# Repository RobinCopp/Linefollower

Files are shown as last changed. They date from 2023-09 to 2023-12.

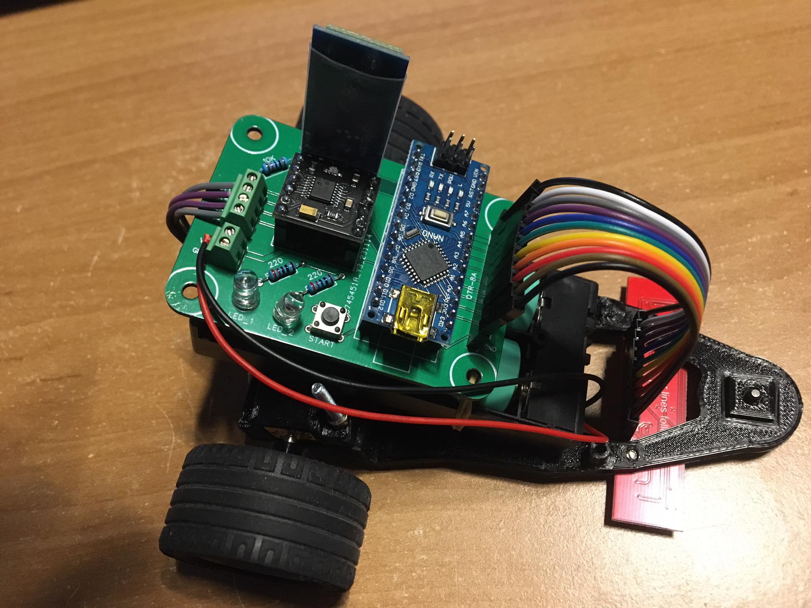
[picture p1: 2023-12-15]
images/367906358_393842836311221_281321537537603859_n.jpg

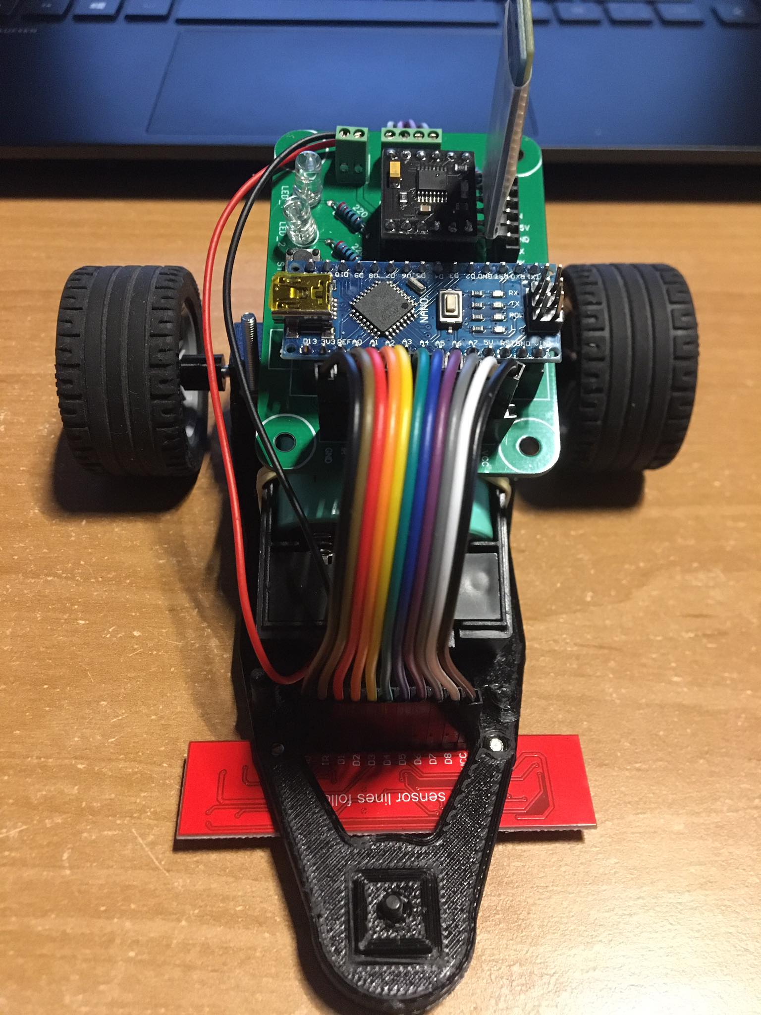
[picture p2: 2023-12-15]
images/385540789_1121335352184012_5968842558492933345_n.jpg

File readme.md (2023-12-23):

# LineFollower



## specifications

microcontroller: Arduino Nano imitatie (ATmega 328P)

motors: Micro Metal Gearmotors (6V 50:1)

h-bridge: DRV8833

sensors: QTR-8A

batteries: 18650 li-ion (2x)

wireless communication: HC-05

distance sensor - motors: 85 mm

weight: 231 g

speed: 0,7 m/s

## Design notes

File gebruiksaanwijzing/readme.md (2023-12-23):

# Gebruiksaanwijzing

### opladen / vervangen batterijen
De twee 18650 li-ion batterijen hebben een speciale oplader nodig. Probeer deze nooit op te laden met een oplader die hier niet voor bedoeld is, dit kan serieuze schade aanrichten.
De batterijhouder wordt op zijn plaats gehouden door enkele elastiekjes. Door deze voorzichtig los te maken kan de batterijhouder van onder de printplaat gehaald worden. Als dit gebeurd is kunnen ze uit de houder gehaald worden en in de oplader gestoken worden. Het is natuurlijk van belang dat de batterijen in de juiste richting in zowel de oplader als in de batterijhouder worden geïnstalleerd. Om de batterijhouder met opgeladen batterijen terug in de auto te installeren moeten de vooraf gaande stappen gewoon in de omgekeerde volgorde uitgevoerd worden.

### draadloze communicatie
#### verbinding maken
Voor draadloze connectie met de auto is een bluethooth module op de auto voorzien. Let op! De bleuthooth module kan niet met Apple apparaten gebruikt worden. Zorg dus dat je een Android toestel ter beschikking hebt. Verder heb je de app "Serial Bluetooth Terminal" nodig om commando's naar de auto te sturen. Verbind eerst via de instellingen van uw apparaat met de bluethoothmodule en selecteer deze vervolgens in de app. Hierna is alles klaar voor het gebruik van draadloze communicatie.

#### commando's
debug [on/off]  = Geeft de ingestelde parameters weer

run  = Starten van de auto (begint te rijden)

stop  = Stoppen van de auto

set cycle [µs]  = Een tijd instellen hoelang de cyclus mag duren. Ongeveer dubbel de calculation time. Deze wordt weergegeven bij debug

set power [0..255]  = Vermogen instellen van de motoren, zet dit niet zomaar op max, de auto zal enkel wheelies trekken

set diff [0..1]  = Het snelheids verschil van de auto tussen de rechte stukken en de bochten. Hoe hoger, hoe minder de auto in de bochten vertraagd

set kp [0..]  = Dit heeft een invloed op hoe "agressief de auto instuurt". Als deze te hoog staat zal de auto heen en weer over de lijn schokken

set ki [0..]  = Zal meer bijsturen hoelanger de bocht

set kd [0..]  = Corrigeert "kp", hoe groter de fout bij "kp", hoe meer er wordt gecorigeerd

calibrate black  = moet uitgevoerd worden als de sensor op een zwart oppervlak staat, hierdoor weet de auto wat zwart is en wat hij straks zal moeten volgen

calibrate white  = moet uitgevoerd worden als de sensor op een wit oppervlak staat, hierdoor weet de auto wat wit is

### kalibratie
Kalibratie moet uitgevoerd worden voor de auto begint te rijden, en moet op het zelfde soort oppervlak gebeuren als de auto straks op zal rijden en moet op de correcte kleur gebeuren, niet op een kleur die er een beetje op trekt.

Eenmaal de auto op de correcte kleur staat, stuur de commando's "calibrate black" en "calibrate white" door naar de auto zoals in de vorige rubriek uitgelegd.

### settings
De robot rijdt stabiel met volgende parameters:

cycle time: 3000

power: 72

diff: 0.74

kp: 20

ki: 0

kd: 0.90

### start/stop button
Na de batterijspanning aan te leggen met de schakelaar die zich vooraan op de batterijhouder bevindt kan op de startknop gedrukt worden om de auto te doen rijden. Deze bevindt zich langs de rechterkant in het midden van de printplaat. Als u erin slaagt om op dezelfde knop te drukken terwijl de auto aan het rijden is, zal deze knop de auto ook weer doen stoppen.

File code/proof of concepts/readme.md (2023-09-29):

# Proof of Concepts

Een proof of concept is een combinatie van minimale hard- en software om eenvoudig aan te tonen dat iets werkt.  
Proof of concepts kunnen enerzijds als eerste poging dienen om een bepaald onderdeel van het project werkend te krijgen. Anderzijds kunnen ze tijdens het debuggen van het finale project dienen als test om eventuele hardware problemen te elimineren bij onduidelijke problemen.
<br />  
<br />
Een proof of concept bestaat uit
* een elektronisch schema (indien van toepassing)
* minimale code om de voorop gestelde zaken te demonstreren
* minimale uitleg / aandachtspunten
<br />
De elektronische schakelingen van de proof of concepts komen bij voorkeur overeen met deze van de uiteindelijke linefollower, zodat de code zonder aanpassingen op het finale project kan draaien.

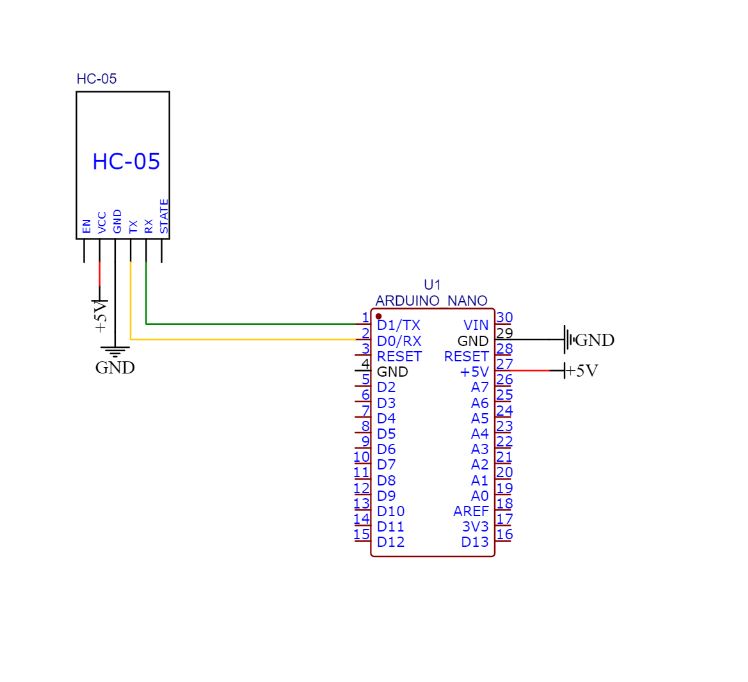
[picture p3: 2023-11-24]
code/proof of concepts/wireless communication/Bluetooth.JPG

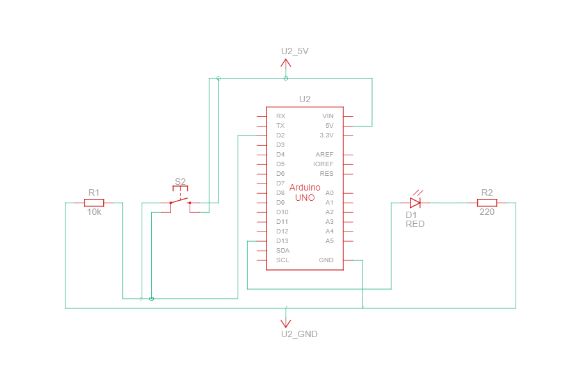
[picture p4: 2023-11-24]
code/proof of concepts/interrupt/Interrupt.JPG

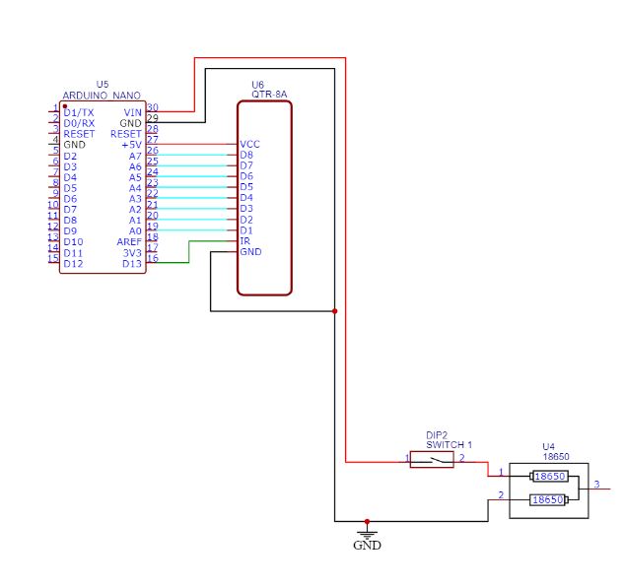
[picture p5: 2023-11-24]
code/proof of concepts/sensor/Sensoren_Schema.JPG

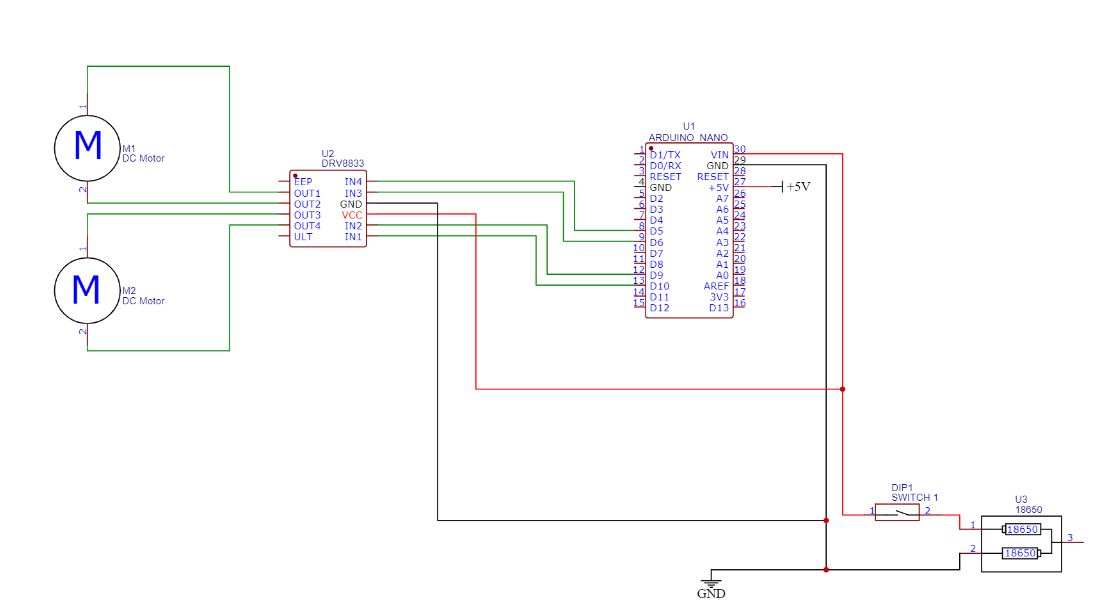
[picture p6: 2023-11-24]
code/proof of concepts/hbridge/H-Brug.JPG

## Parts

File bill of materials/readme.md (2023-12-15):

## bill of materials
<br />

|volgnummer|naam|omschrijving|nieuw/recup|kostprijs/stuk|aantal|subtotaal|
|---|----|---|---|---|---|---|
| 1|  Microcontroller | ATMega 328P |  Nieuw |  €2,61 |  1 | €2,61 |
| 2|  Sensoren  |  QTR-8A |  Nieuw |  €1,24 | 1 |  €1,24 |
| 3|  H-Brug  |  DRV8833 |  Nieuw |  €0,48 |  1 |  €0,48 |
| 4|  Motoren  |  Geared 6V 50:1 |  Nieuw | €3,25 |  2 | €6,50 |
| 5|  Bluethooth  | HC-05 |  Nieuw |  €3,90 | 1 | €3,90 |
| 6|  Batterij  | 18650 | Nieuw |  €3,50 |  2 |  €7 |
| 7|  Batterij Houder  |  Houder |  Recup |  €0 |  1 |  €0 |
| 8|  Batterij Oplader |  Oplader |  Nieuw |  €3,69 |  1 |  €3,69 |
| 9|  Weerstanden  |  10k en 220 |  Recup | €0 | 3 |  €0 |
| 10|  Led  |  Led |  Recup |  €0 |  2 |  €0 |
| 11|  Knop  |  Drukknop | Recup | €0 |  1 |  €0 |
| 12|  Kabels  |  Dupont kabels | Nieuw |  €1,25 |  1 |  €1,25 |
| 13|  Printplaat  |  Custom |  Nieuw |  €5 | 1 |  €5 |
| 14|  PinHeaders  | Pinheaders |  Nieuw |  €2,22 | 1 |  €2,22 |
| 15|  Wielen  |  Lego + 3Dprinted adapter |  Recup |  €0 | 2 | €0 |
| 16|  Chassis  |  3Dprinted |  Nieuw |  €0,65 |  1 |  €0,65 |
| 17|  Boutjes + Moertjes  | M3 | Recup |  €0 | 7 |  €0 |
| | | | | | TOTAAL |  €34,54 |

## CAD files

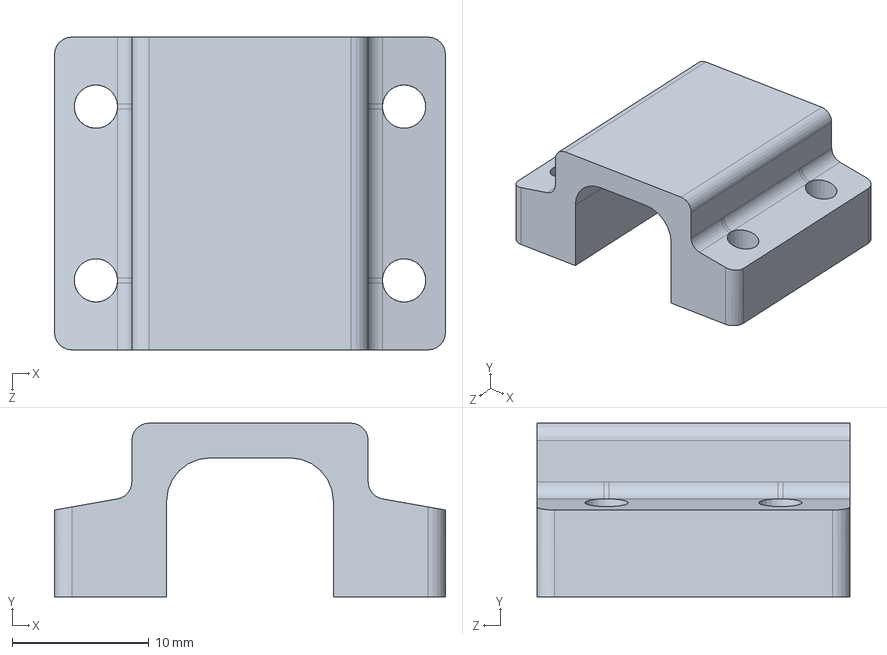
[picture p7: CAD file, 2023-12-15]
technische tekeningen/mechanisch/motor_mount_v2.1.1_straight.SLDPRT
28.6 x 12.7 x 22.9 mm

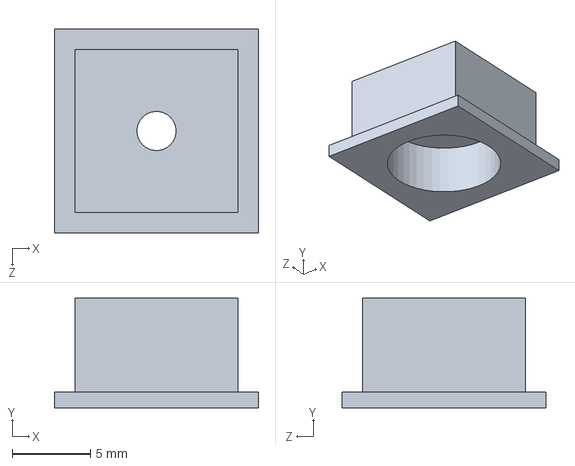
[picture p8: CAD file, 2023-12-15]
technische tekeningen/mechanisch/FRONT_LEG_ADAPTER.SLDPRT
13.0 x 7.00 x 13.0 mm

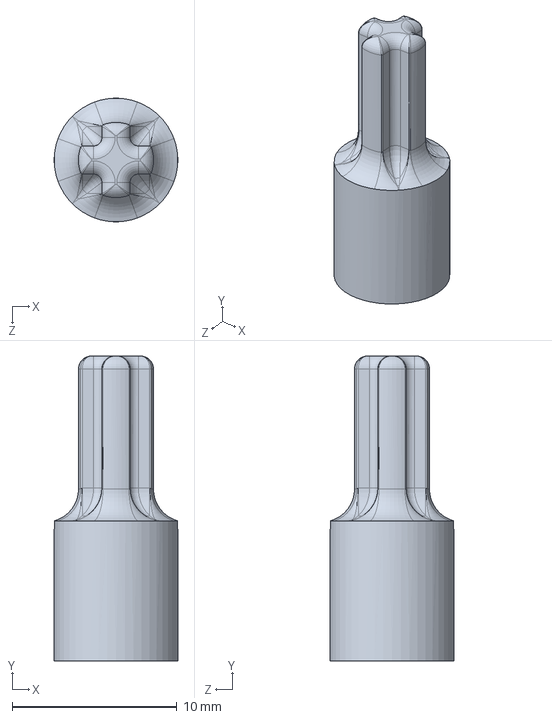
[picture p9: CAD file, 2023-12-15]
technische tekeningen/mechanisch/WielAdapter.SLDPRT
7.50 x 18.5 x 7.50 mm

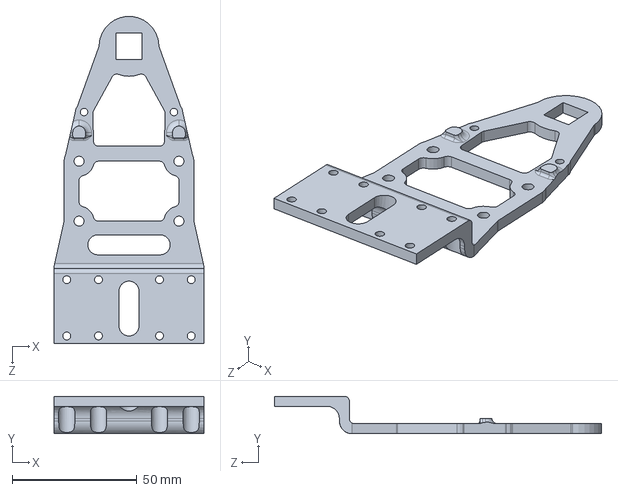
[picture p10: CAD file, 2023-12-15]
technische tekeningen/mechanisch/Synth_Chassis.SLDPRT
60.0 x 15.0 x 130.9 mm

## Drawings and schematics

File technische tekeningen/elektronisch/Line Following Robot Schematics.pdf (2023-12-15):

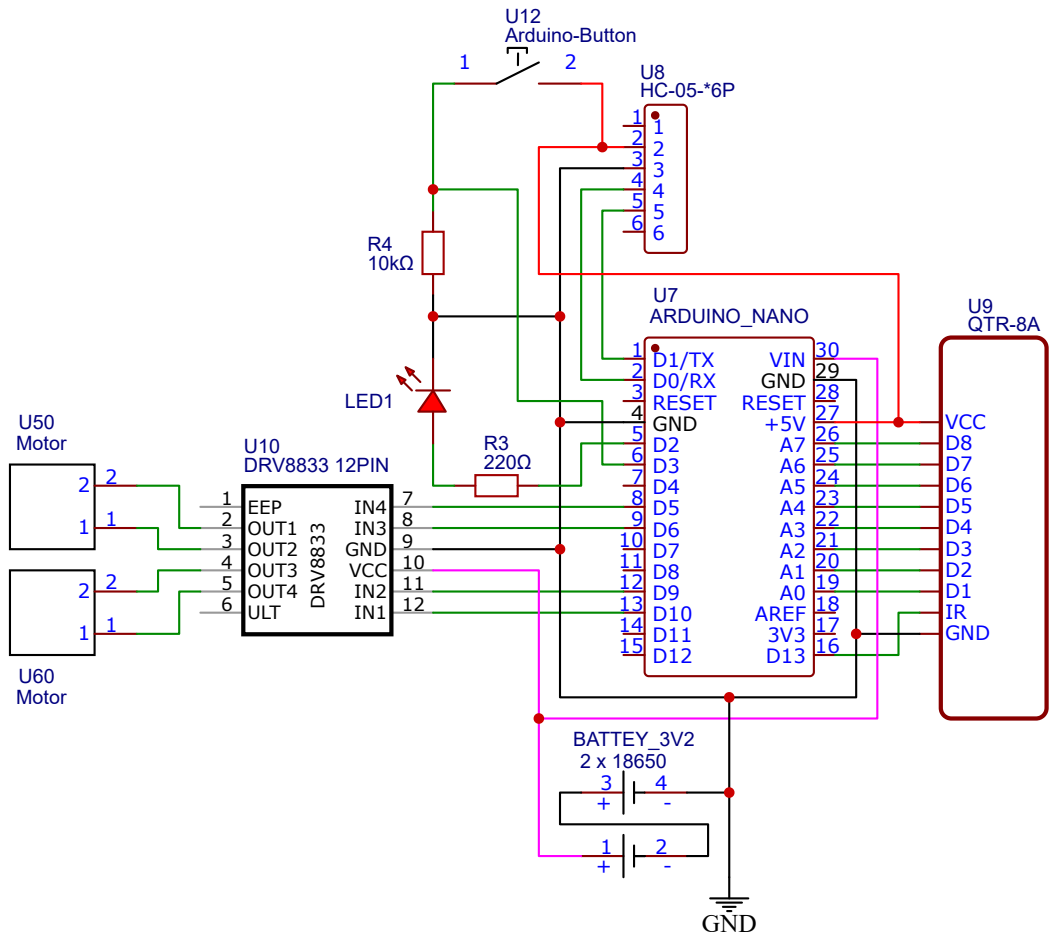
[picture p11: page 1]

Drawn By: Robin Coppens

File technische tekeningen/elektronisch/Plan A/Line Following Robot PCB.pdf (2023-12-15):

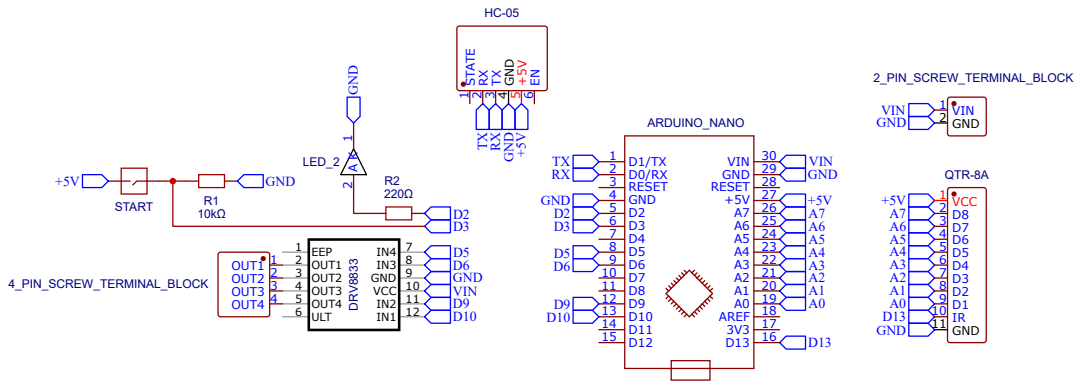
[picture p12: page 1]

Drawn By: Robin Coppens

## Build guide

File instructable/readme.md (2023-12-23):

# Instructable

Een instructable is een stappenplan - zonder verdere uitleg - hoe je vertrekkend van de bill of materials en gebruik makend van de technische tekeningen de robot kan nabouwen. Ook de nodige stappen om de microcontroller te compileren en te uploaden staan beschreven.  

### stap 1
bestel alle componenten uit de bill of materials (bekijk eerst welke je misschien al hebt liggen)

### stap 2
Test of alle componenten ook effectief zoals geadverteerd werken. Hiervoor kunnen de proof of concepts gebruikt worden.

### stap 3
Monteer alle componenten op de printplaat. Voor de microcontroller, H-brug, sensor, bluethooth module, batterijspanning en motoraansluitingen zijn pinheaders voorzien zodat deze zeer gemakkelijk aan te sluiten / af te koppelen zijn.

### stap 4
Het chassis moet je 3D printen. De bestanden hiervoor zijn terug te vinden bij de mechanische technische tekeningen.
Verder moeten ook de motorhouders en de wiel adapters geprint worden.

### stap 5
Soldeer kabels aan de connectors van de motoren om deze op de printplaat te kunnen aansluiten. Gebruik hiervoor geen dikke kabels, aangezien deze de neiging hebben de connectors aan de motor te laten afbreken.

### stap 6
Monteer nu de motoren op het chassis. De motorhouders zet je vast met M3 boutjes. De sensor mag nu ook aan de onderkant van de auto gemonteerd worden. Hiervoor zijn 2 gaten voorzien aan de voorkant van de auto om de M3 boutjes in te draaien. Monteer de sensor zodanig dat de effectieve sensoren aan de voorkant van de auto staan. De pinnen om de sensor aan te sluiten komen nu door het hiervoor voorziene gat uit aan de bovenkant van de auto.

### stap 7
Nu kan de batterijhouder met gemonteerde batterijen op de auto gelegd worden. Deze wordt vastgehouden door een elastiekje, wat het mogelijk maakt deze zeer snel te monteren / demonteren.

### stap 8
De gemonteerde printplaat komt bovenop de batterijhouder en wordt vastgehouden door zowel de sensorkabels vanvoor als de motorkabels vanachter. Hierdoor zweeft de printplaat boven de batterijen.

### stap 9
Nu kunnen de "geleende" Lego Technic wielen op de auto gemonteerd worden. Monteer hiervoor eerst de geprinte wieladapters in de wielen zelf, en schuif ze hierna over de motoren. 

### stap 10
Proficiat! De fysieke auto is klaar. Nu rest ons enkel nog het programma te uploaden naar de microcontroller. Demonteer hiervoor eerst de bluetooth module van de printplaat en plug de auto dan in een usb poort van uw computer. Het Arduino programma kan je vinden onder code -> finaal. Stel als microcontroller de "Atmel atmega 328p" in, en upload het programma. Als dit gelukt is mag de bluetooth module terug gemonteerd worden.

### stap 11
De auto staat nu volledig klaar voor gebruik en moet enkel nog ingesteld worden. Zet de auto op het parcours en maak er verbinding met via bluetooth.
Hoe dit moet en hoe de parameters moeten ingesteld worden is weer te vinden in de gebruiksaanwijzing.

### stap 12
Als al deze stappen gelukt zijn zou dit het resultaat moeten zijn dat je hebt bekomen:






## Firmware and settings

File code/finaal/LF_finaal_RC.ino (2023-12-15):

#include "SerialCommand.h"
#include "EEPROMAnything.h"

#define SerialPort Serial
#define Baudrate 9600

#define MotorLeftForward 6
#define MotorLeftBackward 5
#define MotorRightForward 9
#define MotorRightBackward 10


const int Drukknop = 12;//interupt
const int LED = 2; //Led
const int IR =13; //SensorLED

//interupt:
volatile bool runState = false;
volatile unsigned long lastDebounceTime = 0;  // Tijd voor debouncing
unsigned long debounceDelay = 50;  // Debounce-tijd in milliseconden


SerialCommand sCmd(SerialPort);
bool debug;
bool run;                   
unsigned long previous, calculationTime;


const int sensor[] = {22, 19, A5, A4, A3, A2, A1, A0};


struct param_t
{
  unsigned long cycleTime;
  int black[8];
  int white[8];
  float diff;
  float kp;
  int power;
  float ki;
  float kd;

} params;

int normalised[8];
float debugposition;
float output;
float error;
float iTerm = 0;
float lastErr;


void setup()
{

  pinMode(10, OUTPUT);
  pinMode(9, OUTPUT);
  pinMode(6, OUTPUT);
  pinMode(5, OUTPUT); 

  SerialPort.begin(Baudrate);

  sCmd.addCommand("set", onSet);
  sCmd.addCommand("debug", onDebug);
  sCmd.addCommand("calibrate", onCalibrate);
  sCmd.addCommand("run", onRun);
  sCmd.addCommand("stop", onStop);
  sCmd.setDefaultHandler(onUnknownCommand);

  EEPROM_readAnything(0, params);
  SerialPort.println("ready");

  //Interupt
  pinMode(Drukknop, INPUT);
  attachInterrupt(digitalPinToInterrupt(Drukknop), Interrupt, RISING);

  pinMode(LED, OUTPUT);

  pinMode(IR, OUTPUT);
  digitalWrite(IR, HIGH);
}


void loop()
{
  sCmd.readSerial();
 
  unsigned long current = micros();
  if (current - previous >= params.cycleTime)
  {
    previous = current;
    //normalize
    for (int i = 0; i < 8; i++)
    {
      normalised[i] = map(analogRead(sensor[i]), params.black[i], params.white[i], 0, 1000);
      
    }

    //interpolatie
    int index = 0;
    float position;

    for (int i = 1; i < 8; i++) if (normalised[i] < normalised[index]) index = i;

    if (normalised[index] > 1200) run = false;
    

    if (index == 0) position = -30;
    else if (index == 7) position = 30;
    else
    {
      int sNul = normalised[index];
      int sMinEen = normalised[index-1];
      int sPlusEen = normalised[index+1];

      float b = sPlusEen - sMinEen;
      b = b / 2;

      float a = sPlusEen - b - sNul;

      position = -b / (2 * a);
      position += index;
      position -= 3.5;

      position *= 9.525; //afstand sensoren uit elkaar waarschijnlijk aanpassen

    }
    
    debugposition = position;
    
    //P-regelaar
    error = -position;
    output = error * params.kp;

    //I-Regelaar
    iTerm += params.ki * error;
    iTerm = constrain(iTerm, -510, 510);
    output += iTerm;

    //D-Regelaar
    output += params.kd * (error - lastErr);
    lastErr = error;

    output = constrain(output, -510, 510);

    int powerLeft = 0;
    int powerRight = 0;


    if (run) if (output >= 0)
    {
      powerLeft = constrain(params.power + params.diff * output, -255, 255);
      powerRight = constrain(powerLeft - output, -255, 255);
      powerLeft = powerRight + output;
    }
    else
    {
      powerRight = constrain(params.power - params.diff * output, -255, 255);
      powerLeft = constrain(powerRight + output, -255, 255);
      powerRight = powerLeft - output;
        
    }

    analogWrite(MotorLeftForward, powerLeft > 0 ? powerLeft : 0);
    analogWrite(MotorLeftBackward, powerLeft < 0 ? -powerLeft : 0);
    analogWrite(MotorRightForward, powerRight > 0 ? powerRight : 0);
    analogWrite(MotorRightBackward, powerRight < 0 ? -powerRight : 0);
  }
  
  unsigned long difference = micros() - current;
  if (difference > calculationTime) calculationTime = difference;

}

void onUnknownCommand(char *command)
{
  SerialPort.print("unknown command: \"");
  SerialPort.print(command);
  SerialPort.println("\"");
}


void onSet()
{
  char* param = sCmd.next();
  char* value = sCmd.next();  
  
  if (strcmp(param, "cycle") == 0)
  {
    long newCycleTime = atol(value);
    float ratio = ((float) newCycleTime) / ((float) params.cycleTime);

    params.ki *= ratio;
    params.kd /= ratio;

    params.cycleTime = newCycleTime;
  }

  else if (strcmp(param, "ki") == 0)
  {
    float cycleTimeInSec = ((float) params.cycleTime) / 1000000;
    params.ki = atof(value) * cycleTimeInSec;
  }

  else if (strcmp(param, "kd") == 0)
  {
    float cycleTimeInSec = ((float) params.cycleTime) / 1000000;
    params.kd = atof(value) / cycleTimeInSec;
  }

  else if (strcmp(param, "power") == 0) params.power = atol(value);
  else if (strcmp(param, "diff") == 0) params.diff = atof(value);
  else if (strcmp(param, "kp") == 0) params.kp = atof(value);

  EEPROM_writeAnything(0, params);
}

void onDebug()
{
  SerialPort.print("cycle time: ");
  SerialPort.println(params.cycleTime);
  
  /* parameters weergeven met behulp van het debug commando doe je hier ... */
  SerialPort.print("black: ");
  for (int i = 0; i < 8; i++)
  {
    SerialPort.print(params.black[i]);
    SerialPort.print(" ");
  }
  SerialPort.println(" ");

  SerialPort.print("white: ");
  for (int i = 0; i < 8; i++)
  {
    SerialPort.print(params.white[i]);
    SerialPort.print(" ");
  }
  SerialPort.println(" ");

  SerialPort.print("Normalised: ");
  for (int i = 0; i < 8; i++)
  {
    SerialPort.print(normalised[i]);
    SerialPort.print(" ");
  }
  SerialPort.println(" ");

  SerialPort.print("position: ");
  SerialPort.println(debugposition);

  SerialPort.print("Power: ");
  SerialPort.println(params.power);

  SerialPort.print("diff: ");
  SerialPort.println(params.diff);

  SerialPort.print("kp: ");
  SerialPort.println(params.kp);

  float cycleTimeInSec = ((float) params.cycleTime) / 1000000;
  float ki = params.ki / cycleTimeInSec;
  SerialPort.print("Ki: ");
  SerialPort.println(ki);

  float kd = params.kd * cycleTimeInSec;
  SerialPort.print("Kd: ");
  SerialPort.println(kd);

  SerialPort.print("RUN: ");
  SerialPort.println(params.kp);
  
  SerialPort.println(" ");
  SerialPort.print("calculation time: ");
  SerialPort.println(calculationTime);
  calculationTime = 0;
}

void onCalibrate()
{
  char* param = sCmd.next();

  if (strcmp(param, "black") == 0)
  {
    SerialPort.print("start calibrating black...");
    for (int i = 0; i < 8; i++) params.black[i] = analogRead(sensor[i]);
    SerialPort.println("done");
  }
  else if (strcmp(param, "white") == 0)
  {
    SerialPort.print("start calibrating white...");
    for (int i =0; i < 8; i++) params.white[i] = analogRead(sensor[i]);
    SerialPort.println("done");
  }

  EEPROM_writeAnything(0, params);
}

void onRun()
{
  run = true;
  digitalWrite(LED, HIGH);
}

void onStop()
{
  run = false;
  digitalWrite(LED, LOW);
}

void Interrupt()
{
  // Lees de status van de drukknop
  int buttonState = digitalRead(Drukknop);

  // Debounce de drukknop met millis
  if ((millis() - lastDebounceTime) > debounceDelay) {
    // Als de knop opgaand is, wissel de status van de LED
    if (buttonState == HIGH) {
      runState = !runState;

      // Schakel de LED in of uit op basis van de nieuwe status
      digitalWrite(LED, runState);
      run = runState;
      iTerm = 0;
    }

    // Update de tijd van de laatste debouncing
    lastDebounceTime = millis();
  }
  
}

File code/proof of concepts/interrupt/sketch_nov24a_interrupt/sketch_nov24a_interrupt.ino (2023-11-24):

const int buttonPin = 4;   // Druknop op pin 4
const int ledPin = 3;      // LED op pin 3

volatile bool ledState = false;  // Huidige status van de LED
volatile unsigned long lastDebounceTime = 0;  // Tijd voor debouncing
unsigned long debounceDelay = 50;  // Debounce-tijd in milliseconden

void setup() {
  pinMode(buttonPin, INPUT_PULLUP);  // Configureer pin 2 als ingang met pull-up weerstand
  pinMode(ledPin, OUTPUT);           // Configureer pin 3 als uitgang

  attachInterrupt(digitalPinToInterrupt(buttonPin), buttonInterrupt, RISING);  // Koppel de interrupt-functie aan de opgaande flank van de drukknop
}

void loop() {
  // Doe hier andere taken die onafhankelijk zijn van de drukknopstatus
}

void buttonInterrupt() {
  // Lees de status van de drukknop
  int buttonState = digitalRead(buttonPin);

  // Debounce de drukknop met millis
  if ((millis() - lastDebounceTime) > debounceDelay) {
    // Als de knop opgaand is, wissel de status van de LED
    if (buttonState == HIGH) {
      ledState = !ledState;

      // Schakel de LED in of uit op basis van de nieuwe status
      digitalWrite(ledPin, ledState);
    }

    // Update de tijd van de laatste debouncing
    lastDebounceTime = millis();
  }
}
